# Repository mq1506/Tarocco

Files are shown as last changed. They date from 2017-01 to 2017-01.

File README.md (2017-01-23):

# Tarocco-Lite
Low current version of the Tarroco board. Utilizes the DRV8801

----------------------------------------------------------------------
Based on the Tarocco (c) by Gino Magarotto

Tarocco-Lite is licensed under a
Creative Commons Attribution-ShareAlike 3.0 Unported License.

You should have received a copy of the license along with this
work.  If not, see <http://creativecommons.org/licenses/by-sa/3.0/>.

----------------------------------------------------------------------
Based upon the Tarroco board

Please buy one and support the creator on https://www.crowdsupply.com/citrus-cnc/tarocco

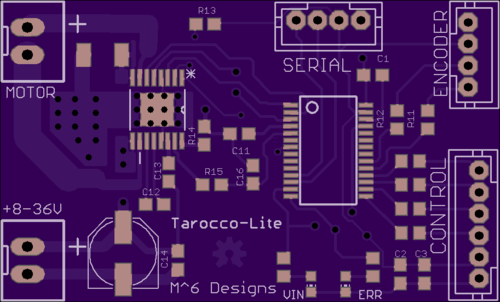
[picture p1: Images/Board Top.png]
Top


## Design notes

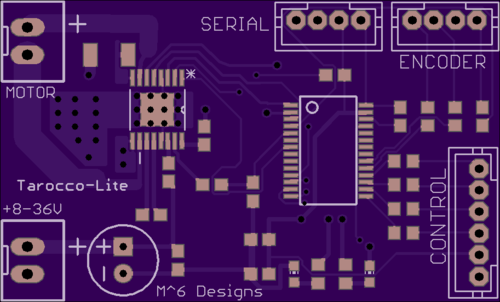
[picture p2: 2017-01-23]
Images/Board Top.jpg

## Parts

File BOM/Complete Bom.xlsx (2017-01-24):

Design Ref | Digi-Key Part Number | Manufacturer | Description | Quantity | Comments | Manufacturer Part Number
C1,C2 | 490-1536-1-ND | MURATA ELECTRONICS (VA) | CAP CER 1UF 16V X5R 0603 | 2 | Alternate Packaging Exists | GRM188R61C105KA93D
C13, C14, C12 | 399-7845-1-ND | KEMET (VA) | CAP CER 0.1UF 50V X7R 0603 | 3 | Alternate Packaging Exists | C0603C104M5RACTU
C3, C11 | 311-1088-1-ND | YAGEO (VA) | CAP CER 0.1UF 16V X7R 0603 | 2 | Alternate Packaging Exists | CC0603KRX7R7BB104
C15 | PCE3917CT-ND | PANASONIC ELECTRONIC COMPONENTS (VA) | CAP ALUM 100UF 20% 50V SMD | 1 | Alternate Packaging Exists | EEE-1HA101UP
C16 | 399-7757-1-ND | KEMET (VA) | CAP CER 1000PF 10V X7R 0402 | 1 | Alternate Packaging Exists | C0402C102K8RACTU
 | CY8C4244PVI-442-ND | CYPRESS SEMICONDUCTOR CORP | IC MCU 32BIT 16KB FLASH 28SSOP | 1 |  | CY8C4244PVI-442
R1, R2 | 311-1.0KGRCT-ND | YAGEO (VA) | RES SMD 1K OHM 5% 1/10W 0603 | 2 |  | RC0603JR-071KL
R7, R8, R9, R10, R11, R12 | 311-330GRCT-ND | YAGEO (VA) | RES SMD 330 OHM 5% 1/10W 0603 | 6 |  | RC0603JR-07330RL
R13, R14 | 311-10KGRCT-ND | YAGEO (VA) | RES SMD 10K OHM 5% 1/10W 0603 | 2 |  | RC0603JR-0710KL
R15 | 311-100KGRCT-ND | YAGEO (VA) | RES SMD 100K OHM 5% 1/10W 0603 | 1 |  | RC0603JR-07100KL
R16 | 73L5R20JCT-ND | CTS RESISTOR PRODUCTS (VA) | RES SMD 0.2 OHM 5% 1/2W 1210 | 1 |  | 73L5R20J
VIN,ERR | 475-2816-1-ND | OSRAM OPTO SEMICONDUCTORS INC(VA) | LED BLUE DIFFUSED 0603 SMD | 2 |  | LB Q39G-L2OO-35-1
 | 296-25378-1-ND | TEXAS INSTRUMENTS (VA) | IC MOTOR DRIVER PAR 16HTSSOP | 1 |  | DRV8801PWPR
 | 455-1706-ND | JST SALES AMERICA INC | CONN HEADER PH TOP 4POS 2MM | 2 |  | B4B-PH-K-S(LF)(SN)
 | 455-1708-ND | JST SALES AMERICA INC | CONN HEADER PH TOP 6POS 2MM | 1 |  | B6B-PH-K-S(LF)(SN)
 | 455-2247-ND | JST SALES AMERICA INC | CONN HEADER XH TOP 2POS 2.5MM | 2 |  | B2B-XH-A(LF)(SN)
 | CY8C4245PVI-482-ND | CYPRESS SEMICONDUCTOR CORP | IC MCU 32BIT 32KB FLASH 28SSOP | 1 |  | CY8C4245PVI-482

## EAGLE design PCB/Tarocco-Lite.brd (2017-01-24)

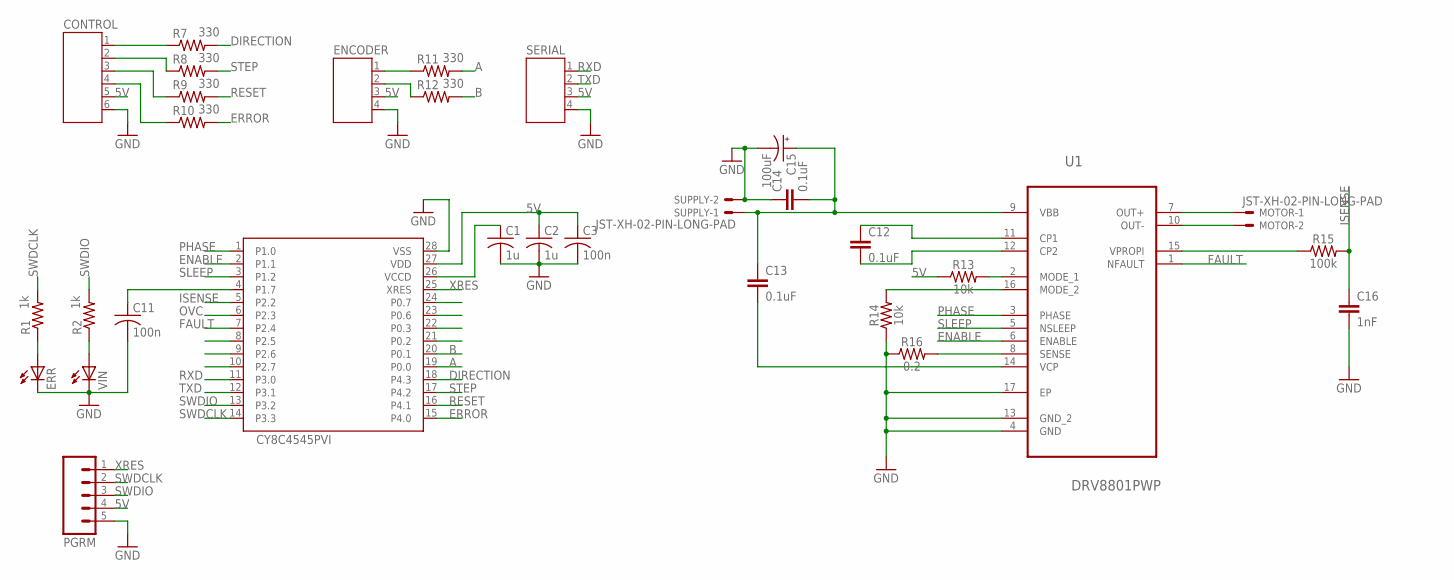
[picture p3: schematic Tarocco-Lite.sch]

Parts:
C1, C2: 1u; C0603
C3, C11: 100n; C0603
C12, C13, C14: 0.1uF; 0603
C15: 100uF; PANASONIC_D
C16: 1nF; 0603
CONTROL: JST-PH6
ENCODER: JST-PH4
ERR: LEDCHIP-LED0603; CHIP-LED0603
IC1: CY8C4545PVI; SSOP28
MOTOR: JST-XH-02-PIN-LONG-PAD; JST-XH-02-PACKAGE-LONG-PAD
PGRM: M05SMD2; 1X05-1MM-RA
R1, R2: 1k; R0603
R7, R8, R9, R10, R11, R12: 330; R0603
R13, R14: 10k; 0603
R15: 100k; 0603
R16: 0.2; 1210
SERIAL: JST-PH4
SUPPLY: JST-XH-02-PIN-LONG-PAD; JST-XH-02-PACKAGE-LONG-PAD
U1: DRV8801PWP; SOP65P640X120-17N
VIN: LEDCHIP-LED0603; CHIP-LED0603

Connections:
5V: C2.1, C3.1, CONTROL.5, ENCODER.3, IC1.27 (VDD), PGRM.4, R13.1, SERIAL.3
A: IC1.19 (P0.0), R11.2
B: IC1.20 (P0.1), R12.2
DIRECTION: IC1.18 (P4.3), R7.2
ENABLE: IC1.2 (P1.1), U1.6 (ENABLE)
ERROR: IC1.15 (P4.0), R10.2
FAULT: IC1.7 (P2.4), U1.1 (NFAULT)
GND: C1.2, C2.2, C3.2, C11.2, C14.1, C15.-, C16.2, CONTROL.6, ENCODER.4, ERR.C, IC1.28 (VSS), PGRM.5, R14.1, R16.1, SERIAL.4, SUPPLY.2, U1.4 (GND), U1.13 (GND_2), U1.17 (EP), VIN.C
ISENSE: C16.1, IC1.5 (P2.2), R15.2
unnamed: ENCODER.1, R11.1
unnamed: R13.2, U1.2 (MODE_1)
unnamed: ENCODER.2, R12.1
unnamed: CONTROL.1, R7.1
unnamed: CONTROL.2, R8.1
unnamed: C1.1, IC1.26 (VCCD)
unnamed: CONTROL.3, R9.1
unnamed: CONTROL.4, R10.1
unnamed: ERR.A, R1.1
unnamed: R2.1, VIN.A
unnamed: R15.1, U1.15 (VPROPI)
unnamed: C12.1, U1.11 (CP1)
unnamed: C11.1, IC1.4 (P1.7)
unnamed: C12.2, U1.12 (CP2)
unnamed: C13.2, U1.14 (VCP)
unnamed: R14.2, U1.16 (MODE_2)
OVC: IC1.6 (P2.3)
PHASE: IC1.1 (P1.0), U1.3 (PHASE)
RESET: IC1.16 (P4.1), R9.2
RXD: IC1.11 (P3.0), SERIAL.1
SENSE: R16.2, U1.8 (SENSE)
SLEEP: IC1.3 (P1.2), U1.5 (NSLEEP)
STEP: IC1.17 (P4.2), R8.2
SWDCLK: IC1.14 (P3.3), PGRM.2, R1.2
SWDIO: IC1.13 (P3.2), PGRM.3, R2.2
TXD: IC1.12 (P3.1), SERIAL.2
VBB: C13.1, C14.2, C15.+, SUPPLY.1, U1.9 (VBB)
VMOT+: MOTOR.1, U1.7 (OUT+)
VMOT-: MOTOR.2, U1.10 (OUT-)
XRES: IC1.25 (XRES), PGRM.1

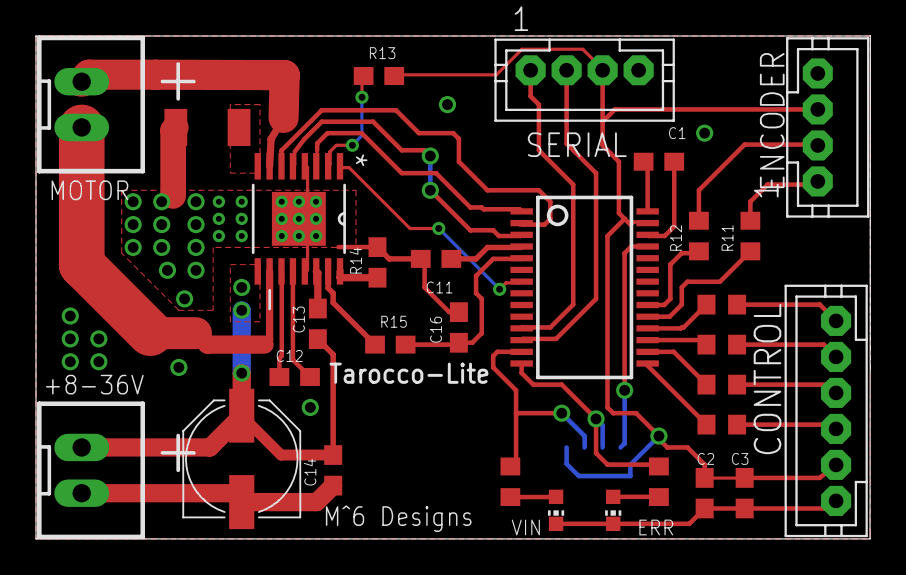
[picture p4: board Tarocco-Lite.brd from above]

Board: 2 copper layers, 46.4 x 27.9 mm, 32 parts (1 on the bottom side), 38 nets.

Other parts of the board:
U$1: OSHW-LOGO-L_COPPER

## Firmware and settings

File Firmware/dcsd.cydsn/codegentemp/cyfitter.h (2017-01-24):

#ifndef INCLUDED_CYFITTER_H
#define INCLUDED_CYFITTER_H
#include "cydevice_trm.h"

/* A */
#define A__0__DM__MASK 0x07u
#define A__0__DM__SHIFT 0u
#define A__0__DR CYREG_PRT0_DR
#define A__0__HSIOM CYREG_HSIOM_PORT_SEL0
#define A__0__HSIOM_MASK 0x0000000Fu
#define A__0__HSIOM_SHIFT 0u
#define A__0__INTCFG CYREG_PRT0_INTCFG
#define A__0__INTSTAT CYREG_PRT0_INTSTAT
#define A__0__MASK 0x01u
#define A__0__PA__CFG0 CYREG_UDB_PA0_CFG0
#define A__0__PA__CFG1 CYREG_UDB_PA0_CFG1
#define A__0__PA__CFG10 CYREG_UDB_PA0_CFG10
#define A__0__PA__CFG11 CYREG_UDB_PA0_CFG11
#define A__0__PA__CFG12 CYREG_UDB_PA0_CFG12
#define A__0__PA__CFG13 CYREG_UDB_PA0_CFG13
#define A__0__PA__CFG14 CYREG_UDB_PA0_CFG14
#define A__0__PA__CFG2 CYREG_UDB_PA0_CFG2
#define A__0__PA__CFG3 CYREG_UDB_PA0_CFG3
#define A__0__PA__CFG4 CYREG_UDB_PA0_CFG4
#define A__0__PA__CFG5 CYREG_UDB_PA0_CFG5
#define A__0__PA__CFG6 CYREG_UDB_PA0_CFG6
#define A__0__PA__CFG7 CYREG_UDB_PA0_CFG7
#define A__0__PA__CFG8 CYREG_UDB_PA0_CFG8
#define A__0__PA__CFG9 CYREG_UDB_PA0_CFG9
#define A__0__PC CYREG_PRT0_PC
#define A__0__PC2 CYREG_PRT0_PC2
#define A__0__PORT 0u
#define A__0__PS CYREG_PRT0_PS
#define A__0__SHIFT 0u
#define A__DR CYREG_PRT0_DR
#define A__INTCFG CYREG_PRT0_INTCFG
#define A__INTSTAT CYREG_PRT0_INTSTAT
#define A__MASK 0x01u
#define A__PA__CFG0 CYREG_UDB_PA0_CFG0
#define A__PA__CFG1 CYREG_UDB_PA0_CFG1
#define A__PA__CFG10 CYREG_UDB_PA0_CFG10
#define A__PA__CFG11 CYREG_UDB_PA0_CFG11
#define A__PA__CFG12 CYREG_UDB_PA0_CFG12
#define A__PA__CFG13 CYREG_UDB_PA0_CFG13
#define A__PA__CFG14 CYREG_UDB_PA0_CFG14
#define A__PA__CFG2 CYREG_UDB_PA0_CFG2
#define A__PA__CFG3 CYREG_UDB_PA0_CFG3
#define A__PA__CFG4 CYREG_UDB_PA0_CFG4
#define A__PA__CFG5 CYREG_UDB_PA0_CFG5
#define A__PA__CFG6 CYREG_UDB_PA0_CFG6
#define A__PA__CFG7 CYREG_UDB_PA0_CFG7
#define A__PA__CFG8 CYREG_UDB_PA0_CFG8
#define A__PA__CFG9 CYREG_UDB_PA0_CFG9
#define A__PC CYREG_PRT0_PC
#define A__PC2 CYREG_PRT0_PC2
#define A__PORT 0u
#define A__PS CYREG_PRT0_PS
#define A__SHIFT 0u

/* B */
#define B__0__DM__MASK 0x38u
#define B__0__DM__SHIFT 3u
#define B__0__DR CYREG_PRT0_DR
#define B__0__HSIOM CYREG_HSIOM_PORT_SEL0
#define B__0__HSIOM_MASK 0x000000F0u
#define B__0__HSIOM_SHIFT 4u
#define B__0__INTCFG CYREG_PRT0_INTCFG
#define B__0__INTSTAT CYREG_PRT0_INTSTAT
#define B__0__MASK 0x02u
#define B__0__PA__CFG0 CYREG_UDB_PA0_CFG0
#define B__0__PA__CFG1 CYREG_UDB_PA0_CFG1
#define B__0__PA__CFG10 CYREG_UDB_PA0_CFG10
#define B__0__PA__CFG11 CYREG_UDB_PA0_CFG11
#define B__0__PA__CFG12 CYREG_UDB_PA0_CFG12
#define B__0__PA__CFG13 CYREG_UDB_PA0_CFG13
#define B__0__PA__CFG14 CYREG_UDB_PA0_CFG14
#define B__0__PA__CFG2 CYREG_UDB_PA0_CFG2
#define B__0__PA__CFG3 CYREG_UDB_PA0_CFG3
#define B__0__PA__CFG4 CYREG_UDB_PA0_CFG4
#define B__0__PA__CFG5 CYREG_UDB_PA0_CFG5
#define B__0__PA__CFG6 CYREG_UDB_PA0_CFG6
#define B__0__PA__CFG7 CYREG_UDB_PA0_CFG7
#define B__0__PA__CFG8 CYREG_UDB_PA0_CFG8
#define B__0__PA__CFG9 CYREG_UDB_PA0_CFG9
#define B__0__PC CYREG_PRT0_PC
#define B__0__PC2 CYREG_PRT0_PC2
#define B__0__PORT 0u
#define B__0__PS CYREG_PRT0_PS
#define B__0__SHIFT 1u
#define B__DR CYREG_PRT0_DR
#define B__INTCFG CYREG_PRT0_INTCFG
#define B__INTSTAT CYREG_PRT0_INTSTAT
#define B__MASK 0x02u
#define B__PA__CFG0 CYREG_UDB_PA0_CFG0
#define B__PA__CFG1 CYREG_UDB_PA0_CFG1
#define B__PA__CFG10 CYREG_UDB_PA0_CFG10
#define B__PA__CFG11 CYREG_UDB_PA0_CFG11
#define B__PA__CFG12 CYREG_UDB_PA0_CFG12
#define B__PA__CFG13 CYREG_UDB_PA0_CFG13
#define B__PA__CFG14 CYREG_UDB_PA0_CFG14
#define B__PA__CFG2 CYREG_UDB_PA0_CFG2
#define B__PA__CFG3 CYREG_UDB_PA0_CFG3
#define B__PA__CFG4 CYREG_UDB_PA0_CFG4
#define B__PA__CFG5 CYREG_UDB_PA0_CFG5
#define B__PA__CFG6 CYREG_UDB_PA0_CFG6
#define B__PA__CFG7 CYREG_UDB_PA0_CFG7
#define B__PA__CFG8 CYREG_UDB_PA0_CFG8
#define B__PA__CFG9 CYREG_UDB_PA0_CFG9
#define B__PC CYREG_PRT0_PC
#define B__PC2 CYREG_PRT0_PC2
#define B__PORT 0u
#define B__PS CYREG_PRT0_PS
#define B__SHIFT 1u

/* ADC_Bypass */
#define ADC_Bypass__0__DM__MASK 0xE00000u
#define ADC_Bypass__0__DM__SHIFT 21u
#define ADC_Bypass__0__DR CYREG_PRT1_DR
#define ADC_Bypass__0__HSIOM CYREG_HSIOM_PORT_SEL1
#define ADC_Bypass__0__HSIOM_MASK 0xF0000000u
#define ADC_Bypass__0__HSIOM_SHIFT 28u
#define ADC_Bypass__0__INTCFG CYREG_PRT1_INTCFG
#define ADC_Bypass__0__INTSTAT CYREG_PRT1_INTSTAT
#define ADC_Bypass__0__MASK 0x80u
#define ADC_Bypass__0__PA__CFG0 CYREG_UDB_PA1_CFG0
#define ADC_Bypass__0__PA__CFG1 CYREG_UDB_PA1_CFG1
#define ADC_Bypass__0__PA__CFG10 CYREG_UDB_PA1_CFG10
#define ADC_Bypass__0__PA__CFG11 CYREG_UDB_PA1_CFG11
#define ADC_Bypass__0__PA__CFG12 CYREG_UDB_PA1_CFG12
#define ADC_Bypass__0__PA__CFG13 CYREG_UDB_PA1_CFG13
#define ADC_Bypass__0__PA__CFG14 CYREG_UDB_PA1_CFG14
#define ADC_Bypass__0__PA__CFG2 CYREG_UDB_PA1_CFG2
#define ADC_Bypass__0__PA__CFG3 CYREG_UDB_PA1_CFG3
#define ADC_Bypass__0__PA__CFG4 CYREG_UDB_PA1_CFG4
#define ADC_Bypass__0__PA__CFG5 CYREG_UDB_PA1_CFG5
#define ADC_Bypass__0__PA__CFG6 CYREG_UDB_PA1_CFG6
#define ADC_Bypass__0__PA__CFG7 CYREG_UDB_PA1_CFG7
#define ADC_Bypass__0__PA__CFG8 CYREG_UDB_PA1_CFG8
#define ADC_Bypass__0__PA__CFG9 CYREG_UDB_PA1_CFG9
#define ADC_Bypass__0__PC CYREG_PRT1_PC
#define ADC_Bypass__0__PC2 CYREG_PRT1_PC2
#define ADC_Bypass__0__PORT 1u
#define ADC_Bypass__0__PS CYREG_PRT1_PS
#define ADC_Bypass__0__SHIFT 7u
#define ADC_Bypass__DR CYREG_PRT1_DR
#define ADC_Bypass__INTCFG CYREG_PRT1_INTCFG
#define ADC_Bypass__INTSTAT CYREG_PRT1_INTSTAT
#define ADC_Bypass__MASK 0x80u
#define ADC_Bypass__PA__CFG0 CYREG_UDB_PA1_CFG0
#define ADC_Bypass__PA__CFG1 CYREG_UDB_PA1_CFG1
#define ADC_Bypass__PA__CFG10 CYREG_UDB_PA1_CFG10
#define ADC_Bypass__PA__CFG11 CYREG_UDB_PA1_CFG11
#define ADC_Bypass__PA__CFG12 CYREG_UDB_PA1_CFG12
#define ADC_Bypass__PA__CFG13 CYREG_UDB_PA1_CFG13
#define ADC_Bypass__PA__CFG14 CYREG_UDB_PA1_CFG14
#define ADC_Bypass__PA__CFG2 CYREG_UDB_PA1_CFG2
#define ADC_Bypass__PA__CFG3 CYREG_UDB_PA1_CFG3
#define ADC_Bypass__PA__CFG4 CYREG_UDB_PA1_CFG4
#define ADC_Bypass__PA__CFG5 CYREG_UDB_PA1_CFG5
#define ADC_Bypass__PA__CFG6 CYREG_UDB_PA1_CFG6
#define ADC_Bypass__PA__CFG7 CYREG_UDB_PA1_CFG7
#define ADC_Bypass__PA__CFG8 CYREG_UDB_PA1_CFG8
#define ADC_Bypass__PA__CFG9 CYREG_UDB_PA1_CFG9
#define ADC_Bypass__PC CYREG_PRT1_PC
#define ADC_Bypass__PC2 CYREG_PRT1_PC2
#define ADC_Bypass__PORT 1u
#define ADC_Bypass__PS CYREG_PRT1_PS
#define ADC_Bypass__SHIFT 7u
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

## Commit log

2017-01-23 Initial Commit of Schematic
    [tarocco.brd, tarocco.sch]
2017-01-23 Starting BRD from scratch
    [tarocco.sch]
2017-01-23 Time to sleep, routing is hard
    [tarocco.brd, tarocco.sch]
2017-01-23 Rename and mostly routed
    [Tarocco-Lite.brd, Tarocco-Lite.sch]
2017-01-23 Alpha finished
    [Tarocco-Lite.brd, Tarocco-Lite.sch]
2017-01-23 Added Image
    [Tarocco-Lite.brd]
2017-01-24 BOM and labelling update
    [Tarocco-Lite.brd, Tarocco-Lite.sch]
2017-01-24 SO MUCH CLEANER
    Cleaned up a lot of the layout to reduce crosstalk
    [Tarocco-Lite.brd, Tarocco-Lite.sch]
2017-01-24 SMD cap swap
    [Tarocco-Lite.brd]
2017-01-24 Moved bootloader location for functionality added proper BOM
    [Complete Bom.xlsx, Tarocco-Lite.brd, cncboot.cyprj.g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]
2017-01-24 ground pour
    [Tarocco-Lite.brd]

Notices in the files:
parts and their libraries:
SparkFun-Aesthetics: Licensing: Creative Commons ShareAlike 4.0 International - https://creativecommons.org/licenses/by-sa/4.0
